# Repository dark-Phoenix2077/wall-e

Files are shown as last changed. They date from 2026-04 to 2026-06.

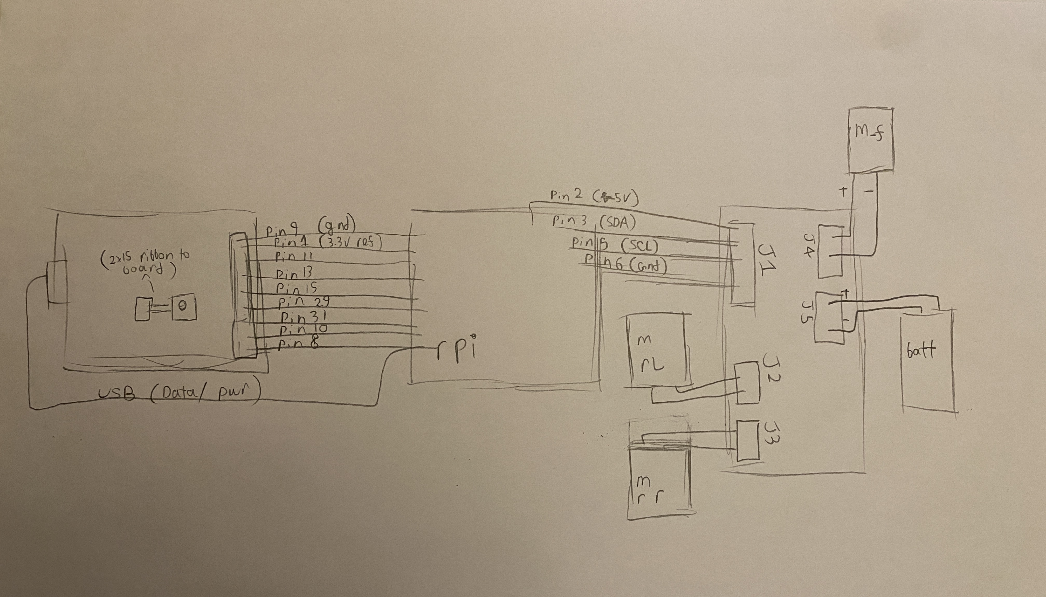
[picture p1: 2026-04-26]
wiring.jpg

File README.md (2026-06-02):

(Just to be clear, I will be paying for this project myself)

# wall-e
a custom smart rover with vision-assisted autonomous navigation and object tracking, built around a Raspberry Pi 3B+ and two fully custom PCB HATs.

Screenshot 2026-04-30 at 5 22 58 pm

# Why I built this
I built this to push myself towards more advanced PCBs and more complex automated systems/ I wanted to try making a fun toy that could also teach me a lot about PCB design and CAD - this being some of my more complex CAD work, especially for the suspension.

# What the project is
Wall-e is a 3D printed rover with custom wheels and suspension powered by a raspberry pi 3b+, as well as two custom PCBs - one for vision, and one for motor control/PD. 

it consists of:

The motor/PD PCB - a tiny little PCB that takes in a battery and 3 motors, and controls them via an ATmega chip, accepting high-level commands from the pi via gpio. it also pushes power to the pi from its own battery:

Screenshot 2026-04-23 at 11 21 24 pm

The vision PCB - a board with an esp32 and a pi camera, as well as usb c and gpio. it communicates mainly via usb c providing a usb camera feed to the pi (translated via the esp32), and uses the gpio for util functions. it has an adressable button (likelly will use for debugging/emergency shutdown purposes) and two status LEDs:

Screenshot 2026-04-23 at 11 23 19 pm

The cad - houses all of it, has a 2 point suspension thingy (idk the proper term):

Screenshot 2026-04-30 at 5 23 22 pm

how the PCBs fit into my design:

Screenshot 2026-06-02 at 9 37 49 pm

Screenshot 2026-06-02 at 10 52 42 pm

Code - currently two test scripts for colour tracking and line following, will start with those and might expand after I get them working - untested on hardware

# BOM

| Board | Line | Designator | Qty | Info | Part | Link |
| :--- | :--- | :--- | :--- | :--- | :--- | :--- |
| Cam hat | 1 | C1, C4, C5, C7, C8, C10 | 6 | - | 10uF MLCC 0805 16V+ | (https://www.lcsc.com/search?q=10uF+0805) |
| Cam hat | 2 | C2 | 1 | - | 100pF MLCC 0402 NP0/C0G | (https://www.lcsc.com/search?q=100pF+0402+C0G) |
| Cam hat | 3 | C3, C6, C9, C11, C12, C13, C14, C15, C16, C17 | 10 | - | 100nF MLCC 0402 | (https://www.lcsc.com/search?q=100nF+0402) |
| Cam hat | 4 | D1 | 1 | Green LED | LED 0603 | (https://www.lcsc.com/search?q=LED+0603+green) |
| Cam hat | 5 | D2 | 1 | Red LED | LED 0603 | (https://www.lcsc.com/search?q=LED+0603+red) |
| Cam hat | 6 | D3 | 1 | - | PRTR5V0U2X,215 | (https://www.lcsc.com/product-detail/C12333.html) |
| Cam hat | 7 | J1 | 1 | USB C | HRO TYPE-C-31-M-12 | (https://www.lcsc.com/search?q=TYPE-C-31-M-12) |
| Cam hat | 8 | J3 | 1 | GPIO | 2.54mm 1x9 pin header | (https://www.lcsc.com/search?q=pin+header+1x9+2.54mm) |
| Cam hat | 9 | J4 | 1 | Mezzanine 2x15 conn (cam) | Hirose DF40C-30DS-0.4V | (https://www.lcsc.com/search?q=DF40C-30DS-0.4V) |
| Cam hat | 10 | R1, R2 | 2 | - | 5.1k resistor 0402 | (https://www.lcsc.com/search?q=5.1k+0402) |
| Cam hat | 11 | R3 | 1 | - | 1M resistor 0402 | (https://www.lcsc.com/search?q=1M+0402+resistor) |
| Cam hat | 12 | R4, R5 | 2 | - | 4.7k resistor 0402 | (https://www.lcsc.com/search?q=4.7k+0402) |
| Cam hat | 13 | R6, R7 | 2 | - | 68 ohm resistor 0402 | (https://www.lcsc.com/search?q=68R+0402+resistor) |
| Cam hat | 14 | R8, R9, R10 | 3 | - | 10k resistor 0402 | (https://www.lcsc.com/search?q=10k+0402) |
| Cam hat | 15 | SW1 | 1 | push button | Tactile switch TL3342 | (https://www.lcsc.com/search?q=TL3342+tactile+switch) |
| Cam hat | 16 | SW2, SW3 | 2 | push button (smaller) | Tactile switch B3U-1000P | (https://www.lcsc.com/search?q=B3U-1000P) |
| Cam hat | 17 | U1 | 1 | - | AMS1117-3.3 | (https://www.lcsc.com/product-detail/C6186.html) |
| Cam hat | 18 | U2 | 1 | - | AMS1117-1.8 | (https://www.lcsc.com/product-detail/C6185.html) |
| Cam hat | 19 | U3 | 1 | - | ESP32-S3 | (https://jlcpcb.com/partdetail/EspressifSystems-ESP32S3/C2913192) |
| Cam hat | 20 | Camera Module | 1 | - | OV5647 5MP CSI Camera Module | (https://www.sunfounder.com/products/ov5647-camera-module) |
| Cam hat | - | PCBA order | - | +94 usd | - | - |
| Motor hat | 21 | C1, C2 | 2 | - | 22pF MLCC 0402 NP0 | (https://www.lcsc.com/search?q=22pF+0402+NP0) |
| Motor hat | 22 | C3, C4, C10, C11, C12, C13, C14, C15 | 8 | - | 100nF MLCC 0402 | (https://www.lcsc.com/search?q=100nF+0402) |
| Motor hat | 23 | C5, C8, C9 | 3 | - | 10uF MLCC 0805 | (https://www.lcsc.com/search?q=10uF+0805) |
| Motor hat | 24 | C6, C16, C17 | 3 | - | 100uF electrolytic / ceramic 1210 | (https://www.lcsc.com/search?q=100uF+1210) |
| Motor hat | 25 | C7 | 1 | - | 220uF electrolytic 1210 | (https://www.lcsc.com/search?q=220uF+1210) |
| Motor hat | 26 | D1 | 1 | - | Schottky diode SMA package | (https://www.lcsc.com/search?q=schottky+diode+SMA) |
| Motor hat | 27 | J1 | 1 | GPIO | 2.54mm 1x4 pin header | (https://www.lcsc.com/search?q=pin+header+1x4+2.54mm) |
| Motor hat | 28 | J2 | 1 | Motor A | JST EH 2-pin vertical | (https://www.lcsc.com/search?q=B2B-EH-A+JST) |
| Motor hat | 29 | J3 | 1 | Motor B | JST EH 2-pin vertical | (https://www.lcsc.com/search?q=B2B-EH-A+JST) |
| Motor hat | 30 | J4 | 1 | Motor C | JST EH 2-pin vertical | (https://www.lcsc.com/search?q=B2B-EH-A+JST) |
| Motor hat | 31 | J5 | 1 | Batt input | JST EH 2-pin vertical | (https://www.lcsc.com/search?q=B2B-EH-A+JST) |
| Motor hat | 32 | J6 | 1 | ISP | 2.54mm 2x3 pin header | (https://www.lcsc.com/search?q=pin+header+2x3+2.54mm) |
| Motor hat | 33 | L1 | 1 | - | Power inductor 2512 | (https://www.lcsc.com/search?q=power+inductor+2512) |
| Motor hat | 34 | R1, R2, R3 | 3 | - | 10k resistor 0402 | (https://www.lcsc.com/search?q=10k+0402) |
| Motor hat | 35 | U1 | 1 | - | ATMEGA328P-AU | (https://www.lcsc.com/product-detail/C14877.html) |
| Motor hat | 36 | U2, U3 | 2 | - | TB6612FNG | (https://www.lcsc.com/product-detail/Motor-Driver-ICs_TOSHIBA-TB6612FNG-C-8-EL_C141517.html) |
| Motor hat | 37 | U4 | 1 | - | LM2596S-5.0/NOPB | (https://www.lcsc.com/product-detail/C116713.html) |
| Motor hat | 38 | U5 | 1 | - | LD1117S33TR | (https://lcsc.com/product-detail/Linear-Voltage-Regulators-LDO_STMicroelectronics-LD1117S33TR_C86781.html) |
| Motor hat | 39 | Y1 | 1 | 16MHz Crystal | X322516MOB4SI 16MHz | (https://www.lcsc.com/product-detail/C12668.html) |
| Motor hat | - | PCBA order | - | +97 usd | - | - |
| Other | 40 | DC 6V Motor | 3 | - | 3V–6V brushed DC toy motor (TT gearmotor) | (https://www.lcsc.com/search?q=DC+motor+toy) |
| Other | 43 | Battery | 1 | for motors and rest of the system | 7.4V 2S LiPo ~1500–2200mAh | (https://www.aliexpress.com/item/1005007342294070.html) |
| Other | 44 | Spring | 4 | for suspension | 35mm × 10mm steel compression springs | (https://www.rays-teksurplus.co.uk/2-x-helical-compression-springs-steel-length-35mm-diameter-10mm-f3-13337-p.asp) |

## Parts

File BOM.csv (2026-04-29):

Board | Designator | Qty | Info | Part | Link | Price (per unit)
Cam hat | C1, C4, C5, C7, C8, C10 | 6 | - | 10uF MLCC 0805 16V+ | https://www.lcsc.com/search?q=10uF+0805 | $0.0154
Cam hat | C2 | 1 | - | 100pF MLCC 0402 NP0/C0G | https://www.lcsc.com/search?q=100pF+0402+C0G | $0.0008
Cam hat | C3, C6, C9, C11, C12, C13, C14, C15, C16, C17 | 10 | - | 100nF MLCC 0402 | https://www.lcsc.com/search?q=100nF+0402 | $0.0009
Cam hat | D1 | 1 | Green LED | LED 0603 | https://www.lcsc.com/search?q=LED+0603+green | $0.0034
Cam hat | D2 | 1 | Red LED | LED 0603 | https://www.lcsc.com/search?q=LED+0603+red | $0.0038
Cam hat | D3 | 1 | - | PRTR5V0U2X,215 | https://www.lcsc.com/product-detail/C12333.html | $2.2145
Cam hat | J1 | 1 | USB C | HRO TYPE-C-31-M-12 | https://www.lcsc.com/search?q=TYPE-C-31-M-12 | $0.1702
Cam hat | J3 | 1 | GPIO | 2.54mm 1x9 pin header | https://www.lcsc.com/search?q=pin+header+1x9+2.54mm | $0.0397
Cam hat | J4 | 1 | Mezzanine 2x15 conn (cam) | Hirose DF40C-30DS-0.4V | https://www.lcsc.com/search?q=DF40C-30DS-0.4V | $0.3630
Cam hat | R1, R2 | 2 | - | 5.1k resistor 0402 | https://www.lcsc.com/search?q=5.1k+0402 | $0.0005
Cam hat | R3 | 1 | - | 1M resistor 0402 | https://www.lcsc.com/search?q=1M+0402+resistor | $0.0005
Cam hat | R4, R5 | 2 | - | 4.7k resistor 0402 | https://www.lcsc.com/search?q=4.7k+0402 | $0.0005
Cam hat | R6, R7 | 2 | - | 68 ohm resistor 0402 | https://www.lcsc.com/search?q=68R+0402+resistor | $0.0005
Cam hat | R8, R9, R10 | 3 | - | 10k resistor 0402 | https://www.lcsc.com/search?q=10k+0402 | $0.0005
Cam hat | SW1 | 1 | push button | Tactile switch TL3342 | https://www.lcsc.com/search?q=TL3342+tactile+switch | $0.7361
Cam hat | SW2, SW3 | 2 | push button (smaller) | Tactile switch B3U-1000P | https://www.lcsc.com/search?q=B3U-1000P | $0.0773
Cam hat | U1 | 1 | - | AMS1117-3.3 | https://www.lcsc.com/product-detail/C6186.html | $0.2139
Cam hat | U2 | 1 | - | AMS1117-1.8 | https://www.lcsc.com/product-detail/C6185.html | $0.2339
Cam hat | U3 | 1 | - | ESP32-S3 | https://jlcpcb.com/partdetail/EspressifSystems-ESP32S3/C2913192 | $3.0345
Cam hat | Camera Module | 1 | - | OV5647 5MP CSI Camera Module | https://www.sunfounder.com/products/ov5647-camera-module | $10.99
Cam hat | PCBA order | - |  | - | - | 112 USD total (including parts)
Motor hat | C1, C2 | 2 | - | 22pF MLCC 0402 NP0 | https://www.lcsc.com/search?q=22pF+0402+NP0 | $0.0012
Motor hat | C3, C4, C10, C11, C12, C13, C14, C15 | 8 | - | 100nF MLCC 0402 | https://www.lcsc.com/search?q=100nF+0402 | $0.0009
Motor hat | C5, C8, C9 | 3 | - | 10uF MLCC 0805 | https://www.lcsc.com/search?q=10uF+0805 | $0.0154
Motor hat | C6, C16, C17 | 3 | - | 100uF electrolytic / ceramic 1210 | https://www.lcsc.com/search?q=100uF+1210 | $0.1770
Motor hat | C7 | 1 | - | 220uF electrolytic 1210 | https://www.lcsc.com/search?q=220uF+1210 | $0.5903
Motor hat | D1 | 1 | - | Schottky diode SMA package | https://www.lcsc.com/search?q=schottky+diode+SMA | $0.0109
Motor hat | J1 | 1 | GPIO | 2.54mm 1x4 pin header | https://www.lcsc.com/search?q=pin+header+1x4+2.54mm | $0.0201
Motor hat | J2 | 1 | Motor A | JST EH 2-pin vertical | https://www.lcsc.com/search?q=B2B-EH-A+JST | $0.0522
Motor hat | J3 | 1 | Motor B | JST EH 2-pin vertical | https://www.lcsc.com/search?q=B2B-EH-A+JST | $0.0522
Motor hat | J4 | 1 | Motor C | JST EH 2-pin vertical | https://www.lcsc.com/search?q=B2B-EH-A+JST | $0.0522
Motor hat | J5 | 1 | Batt input | JST EH 2-pin vertical | https://www.lcsc.com/search?q=B2B-EH-A+JST | $0.0522
Motor hat | J6 | 1 | ISP | 2.54mm 2x3 pin header | https://www.lcsc.com/search?q=pin+header+2x3+2.54mm | $0.0307
Motor hat | L1 | 1 | - | Power inductor 2512 | https://www.lcsc.com/search?q=power+inductor+2512 | $0.0533
Motor hat | R1, R2, R3 | 3 | - | 10k resistor 0402 | https://www.lcsc.com/search?q=10k+0402 | $0.0005
Motor hat | U1 | 1 | - | ATMEGA328P-AU | https://www.lcsc.com/product-detail/C14877.html | $2.6408
Motor hat | U2, U3 | 2 | - | TB6612FNG | https://www.lcsc.com/product-detail/Motor-Driver-ICs_TOSHIBA-TB6612FNG-C-8-EL_C141517.html | $1.1114
Motor hat | U4 | 1 | - | LM2596S-5.0/NOPB | https://www.lcsc.com/product-detail/C116713.html | $1.3616
Motor hat | U5 | 1 | - | LD1117S33TR | https://lcsc.com/product-detail/Linear-Voltage-Regulators-LDO_STMicroelectronics-LD1117S33TR_C86781.html | $0.1783
Motor hat | Y1 | 1 | 16MHz Crystal | X322516MOB4SI 16MHz | https://www.lcsc.com/product-detail/C12668.html | $0.0752
Motor hat | PCBA order | - |  | - | - | 97 USD total (including parts)
Other | DC 6V Motor | 3 | - | 3V–6V brushed DC toy motor (TT gearmotor) | https://ar.aliexpress.com/item/1005005959011446.html?curPageLogUid=mhEIOERclBAs | $0.99
Other | Battery | 1 | for motors and rest of the system | 7.4V 2S LiPo ~1500–2200mAh | https://ar.aliexpress.com/item/1005010067844747.html?curPageLogUid=bqrtZ9YQ4Xe4 | $10.36
Other | Spring | 4 | for suspension | 35mm × 10mm steel compression springs | https://ar.aliexpress.com/item/1005005488967572.html?curPageLogUid=TogT2m8wGbtU | $0.99 (lot of 20)

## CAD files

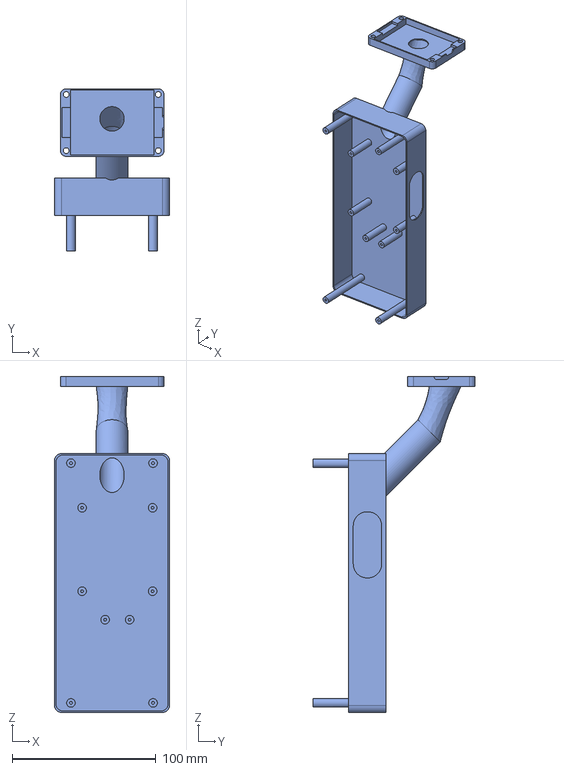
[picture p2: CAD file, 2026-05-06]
CAD/cad_parts/Main housing top.step
80.0 x 112.9 x 233.5 mm

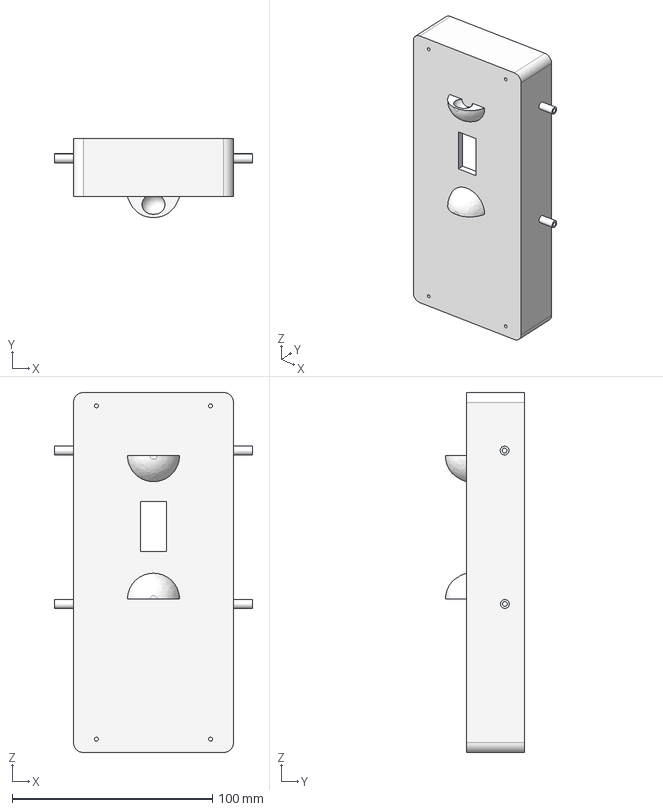
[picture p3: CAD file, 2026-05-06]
CAD/cad_parts/Main housing bottom.step
99.2 x 39.3 x 180.0 mm

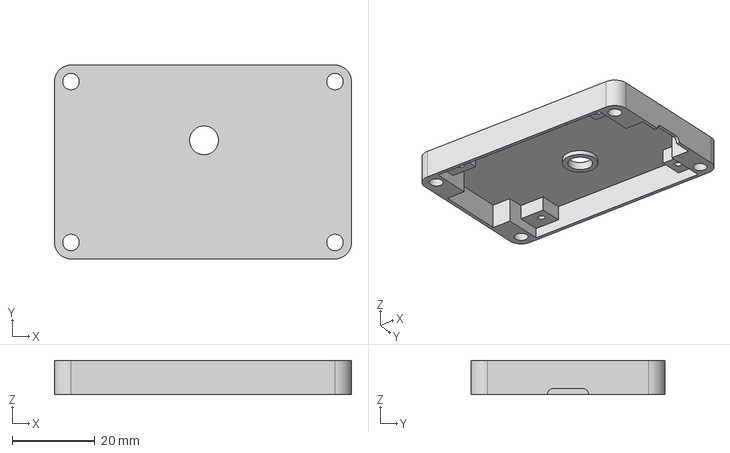
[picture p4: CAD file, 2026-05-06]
CAD/cad_parts/Cam front cover.step
72.0 x 47.0 x 8.30 mm

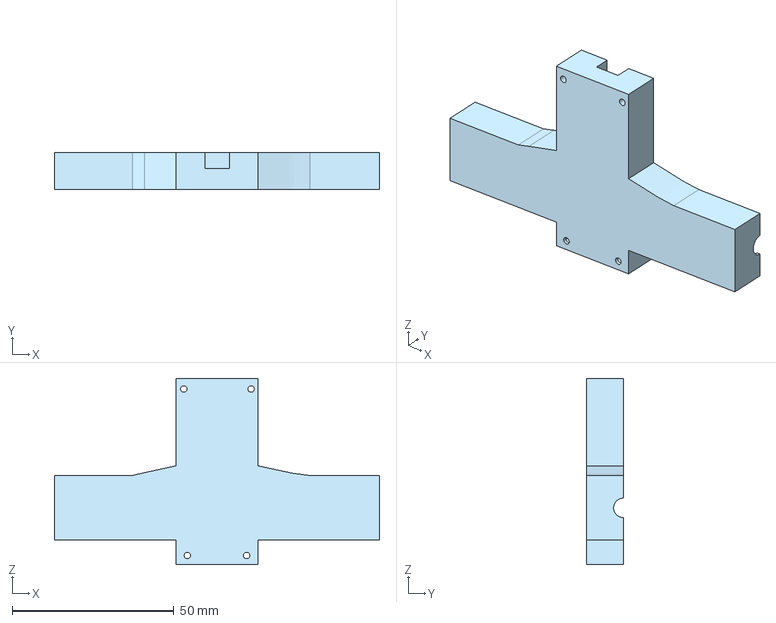
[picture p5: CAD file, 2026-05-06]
CAD/cad_parts/rear motor housing bottom.step
100.4 x 11.3 x 57.6 mm

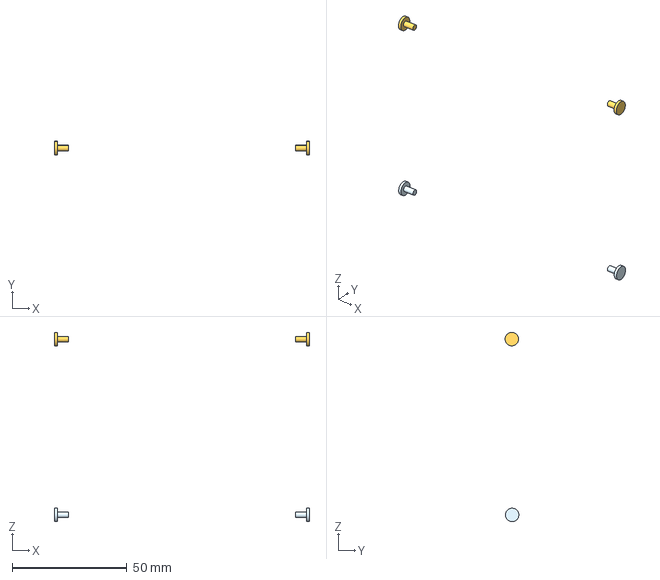
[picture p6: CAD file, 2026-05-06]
CAD/cad_parts/Suspension arm pins.step
111.2 x 6.01 x 82.6 mm

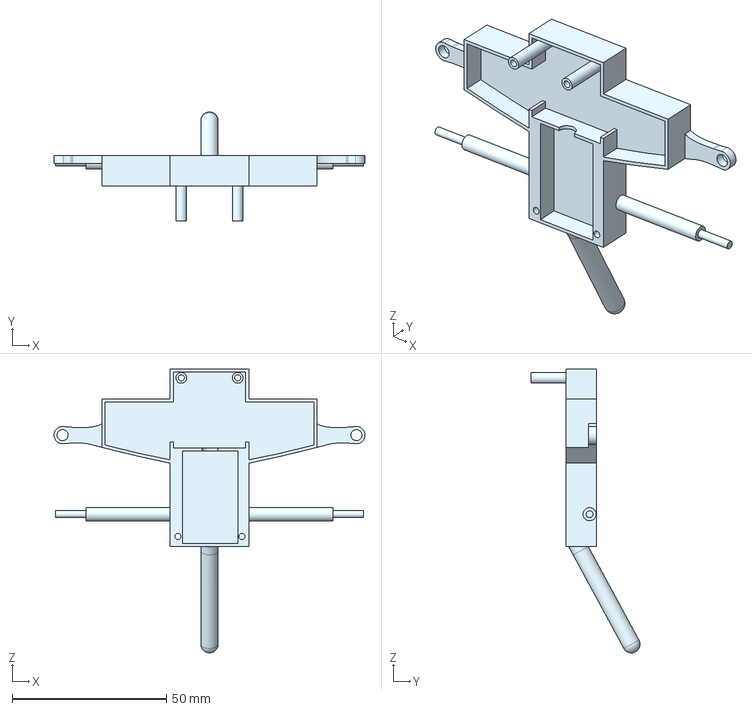
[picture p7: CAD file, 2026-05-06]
CAD/cad_parts/Front motor housing top.step
100.8 x 35.4 x 92.0 mm

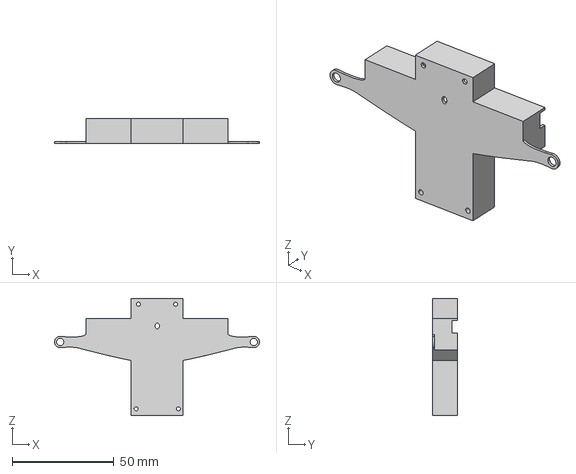
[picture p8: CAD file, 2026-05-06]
CAD/cad_parts/front motor housing bottom.step
100.8 x 12.3 x 57.6 mm

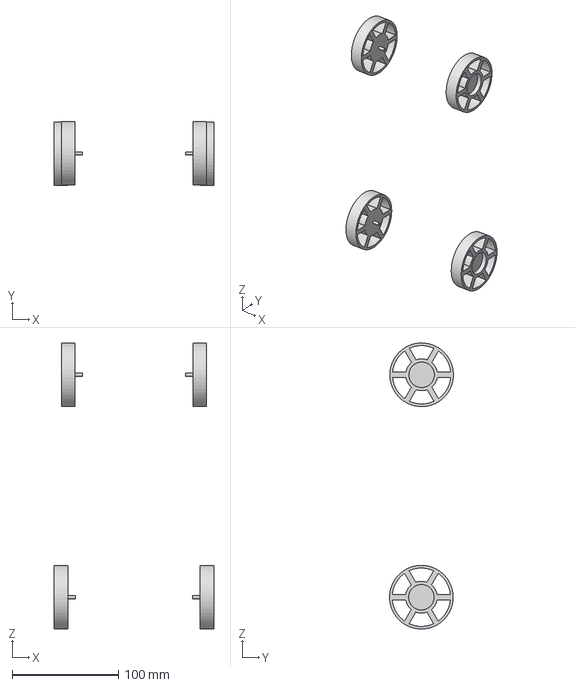
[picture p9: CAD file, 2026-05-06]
CAD/cad_parts/Wheels.step
150.4 x 60.2 x 269.4 mm

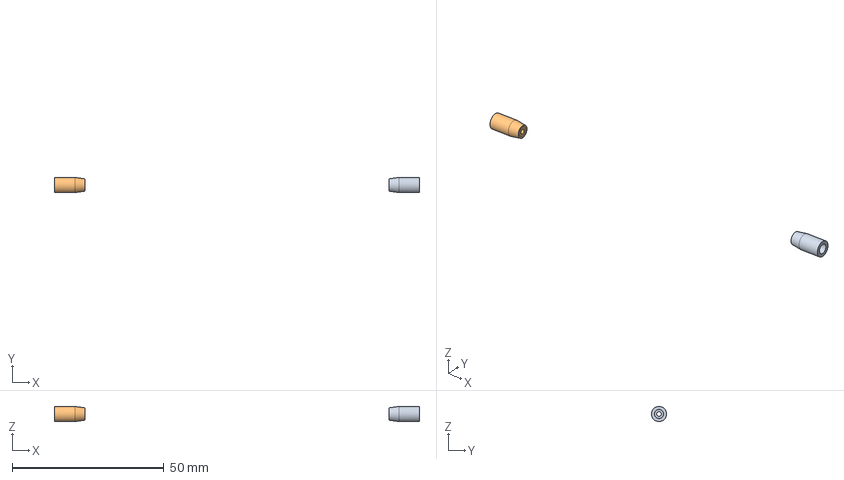
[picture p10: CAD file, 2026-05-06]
CAD/cad_parts/Rear wheel motor-axle adapters.step
120.4 x 5.00 x 5.00 mm

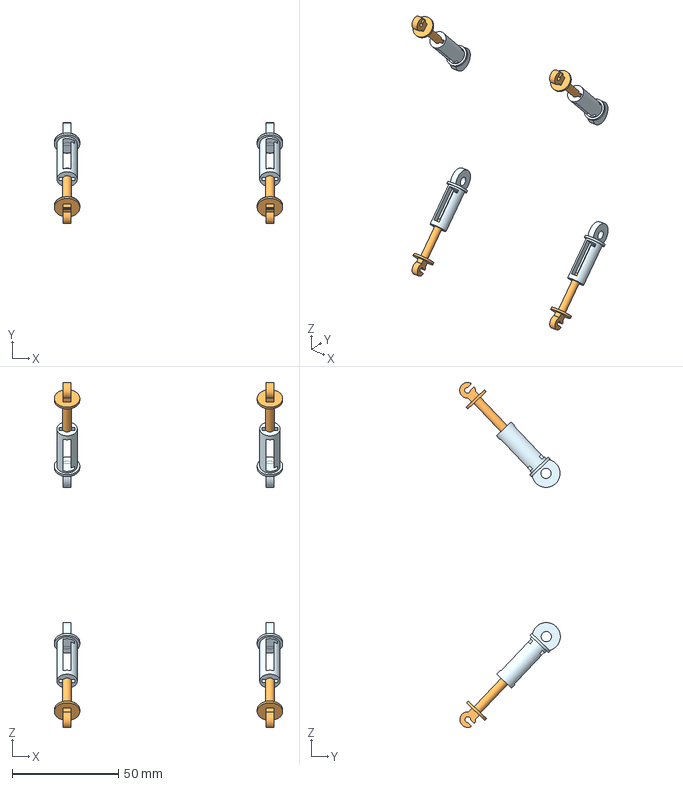
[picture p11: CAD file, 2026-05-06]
CAD/cad_parts/Suspension arms.step
107.3 x 47.3 x 162.0 mm

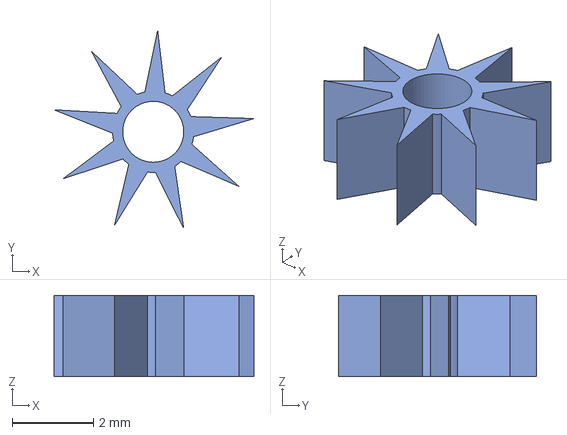
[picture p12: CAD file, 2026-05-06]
CAD/cad_parts/front wheel motor gear.step
4.92 x 4.88 x 2.00 mm

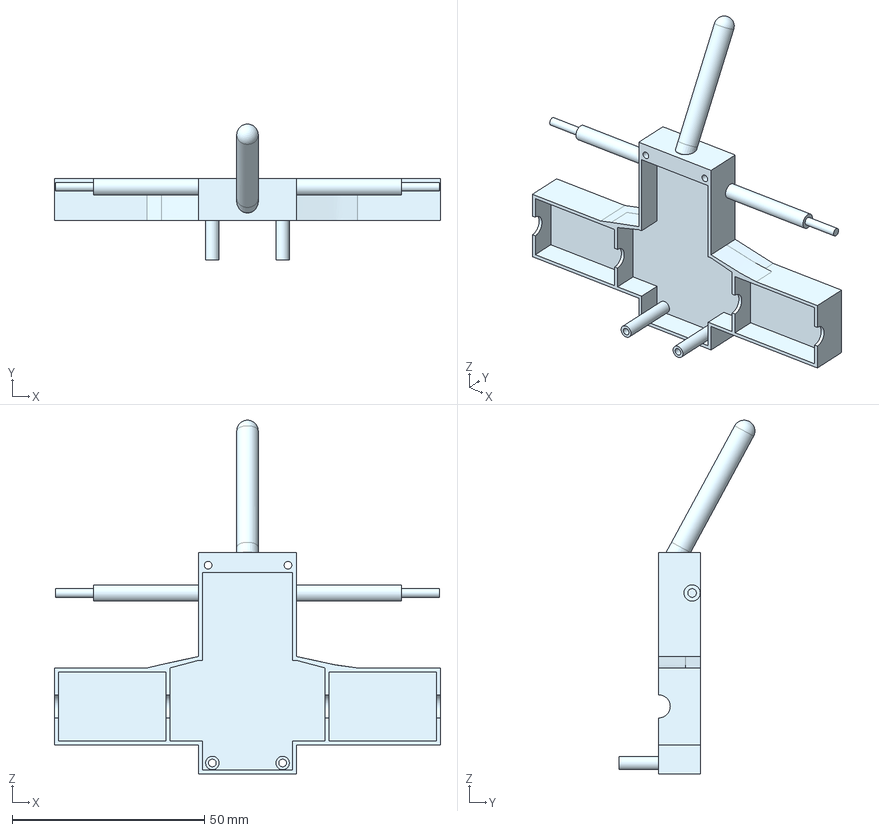
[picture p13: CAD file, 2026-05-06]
CAD/cad_parts/rear motor housing top.step
100.4 x 35.4 x 92.0 mm

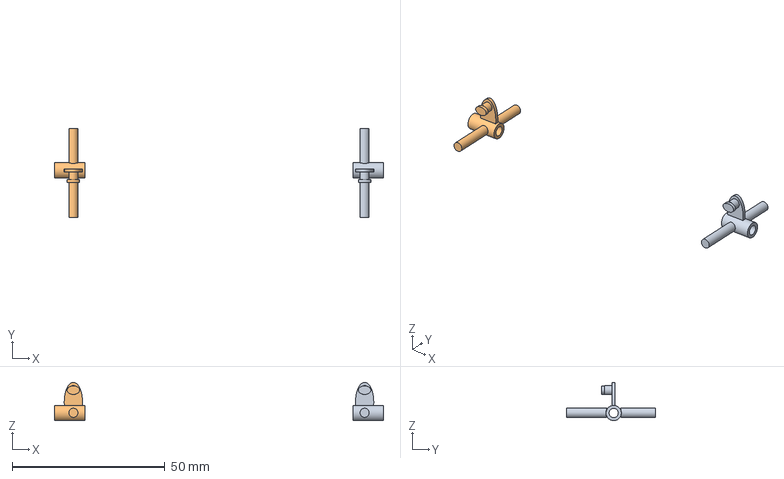
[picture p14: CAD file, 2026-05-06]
CAD/cad_parts/front wheel cranks.step
107.6 x 29.0 x 12.5 mm

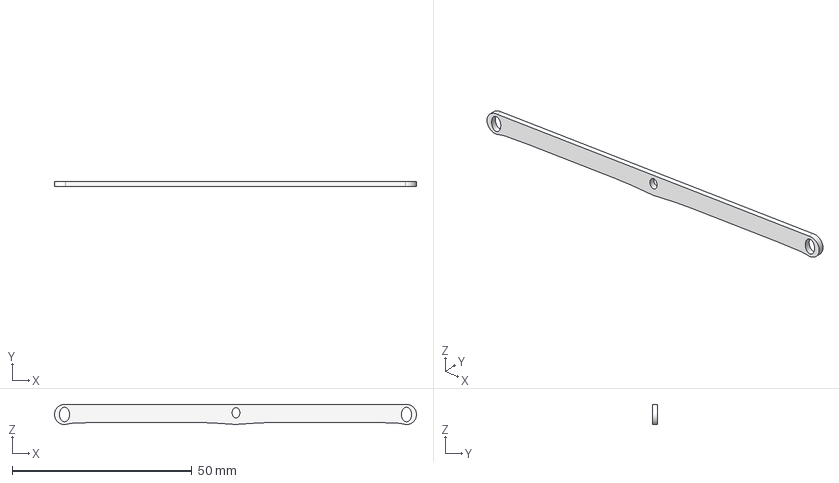
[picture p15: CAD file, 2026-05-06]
CAD/cad_parts/front wheel rot bar.step
100.8 x 1.50 x 5.59 mm

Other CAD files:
CAD/assembly.step
CAD/cad_parts/front wheel rot gear.step

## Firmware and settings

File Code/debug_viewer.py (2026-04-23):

from flask import Flask, Response
import cv2, threading

app = Flask(__name__)
camera = Camera()
lock = threading.Lock()
latest_frame = None

def capture_loop():
    global latest_frame
    while True:
        frame = camera.read()
        if frame is not None:
            with lock:
                latest_frame = frame.copy()

def generate():
    while True:
        with lock:
            if latest_frame is None:
                continue
            _, jpeg = cv2.imencode('.jpg', latest_frame)
        yield (b'--frame\r\nContent-Type: image/jpeg\r\n\r\n' +
               jpeg.tobytes() + b'\r\n')

@app.route('/video')
def video():
    return Response(generate(),
                    mimetype='multipart/x-mixed-replace; boundary=frame')

if __name__ == '__main__':
    t = threading.Thread(target=capture_loop, daemon=True)
    t.start()
    app.run(host='0.0.0.0', port=5000)

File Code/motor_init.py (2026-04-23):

import smbus2, time

class MotorController:
    ADDR = 0x10
    
    def __init__(self):
        self.bus = smbus2.SMBus(1)
    
    def _send(self, cmd):
        self.bus.write_byte(self.ADDR, ord(cmd))
    
    def forward(self):  self._send('F')
    def backward(self): self._send('B')
    def stop(self):     self._send('S')
    def steer_left(self):   self._send('L')
    def steer_right(self):  self._send('R')
    def steer_centre(self): self._send('C')
    
    def speed(self, val):
        val = max(0, min(255, int(val)))
        self.bus.write_byte(self.ADDR, ord('X'))
        self.bus.write_byte(self.ADDR, val)

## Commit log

2026-04-23 added BOM
    [BOM.csv]
2026-04-23 upated CSV
    [BOM.csv]
2026-04-23 added wiring diagram
2026-04-26 cleaned up fluff
    [BOM.csv]
2026-04-26 updated bom
2026-04-26 added wiring drawing (rlly bad, dont judge)
2026-04-26 added new and improved cad
    [wal_e.step]
2026-04-29 added bom prices
    [BOM.csv]
2026-04-29 added new cad with thickened joints on suspension
    (I just thickened anything that seemed really thin, but currently my suspension looks good - it isnt for anything heavy-duty and should hold the robot easily and manage uneven terrain with the spring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
    [wall e.step]
2026-04-30 changed readme cad photos for (hopefully) the last time
2026-04-30 added cad with bigger suspension
    [wall_e_bigger_suspension.step]
2026-04-30 deleted old cad
    [wall e.step]
2026-05-06 renamed assembly cad
    [cad_full_assembly.step]
2026-05-06 added individual part cad files
    [Cam front cover.step, Front motor housing top.step, Main housing bottom.step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]
2026-06-02 added photos of the cad with the PCBs
2026-06-02 deleted assembly without PCBs
    [cad_full_assembly.step]
2026-06-02 Added updated assembly file with PCBs using LFS
    [assembly.step]
2026-06-02 changed camera pcb image with fixed orientation
2026-06-02 deleted assembly with old camera pcb orientation
    [assembly.step]
2026-06-02 Update assembly.step with fixed camera pcb orientation
    [assembly.step]
